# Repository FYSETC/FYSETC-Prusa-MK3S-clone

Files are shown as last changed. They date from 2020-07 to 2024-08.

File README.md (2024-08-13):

# FYSETC-Prusa-MK3S+-clone
FYSETC Prusa MK3S+ clone Kit Database

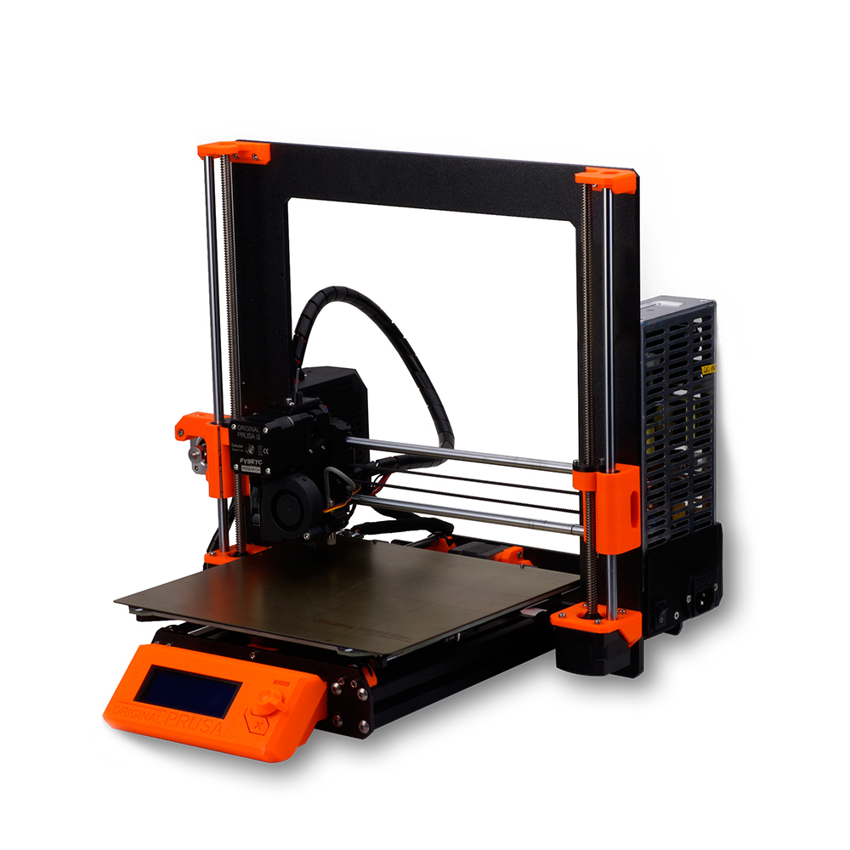
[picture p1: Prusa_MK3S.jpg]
image-Prusa MK3S

1.Prusa MK3S STL file update 2020.7.10
These print files are suitable for FYSETC prusa MK3S 3D printer. Compared with the official printed parts, we have added three parts: PSU-cover-MK3_bottom, PSU-cover-MK3_top, and Spool-holder.The other parts are the same as the official Prusa MK3S. 
You can also get it here：
https://www.thingiverse.com/thing:4728793

2.Prusa MK3S+ assembly tutorial  
<https://help.prusa3d.com/category/original-prusa-i3-mk3s-kit-assembly_1128>

3.Prusa MK3S+ knowledge base  
<https://help.prusa3d.com/en/tag/mk3s+/>

4.Prusa MK3S+ assembly tutorial update 2020.8.3  
The tutorial is very thorough and well explained. We also provide a video tutorial for the assembly process. It is advisable to check both tutorials as you build，below you can watch the video tutorial divided into 5 parts:

https://youtu.be/e2qvbB0Xqfg

https://youtu.be/ntqnIuPzF5k

https://youtu.be/NayX_Eky94o

https://youtu.be/t37JR-865cU

https://youtu.be/UVHUfH4zhIA

5.Go to buy link：https://es.aliexpress.com/item/32968736910.html?spm=a219c.12010615.8148356.3.26ed28558FsEev

# BugFix：
## MK3S+ no Bightness menu fix

### Phenomenon:

Originally, there would be a brightness menu under the setting to adjust the screen backlight, but in fact there isn't;

### Reason:

In order to be more stable during the production of the 2004 screen, we upgraded the triode (BC817) that controls the backlight with a MOS tube (AO3400); The brightness menu will only be available when it is in a low state, so many people who use this screen do not see the brightness menu.

### Solution:

#### 1. Software Method :

Compile the firmware by yourself, and turn off some functions of power-on detection low level.
Open the backlight.cpp file and find the following location:

```cpp
void backlight_init()
{
//check for backlight support on lcd
    SET_INPUT(LCD_BL_PIN);
    WRITE(LCD_BL_PIN,HIGH);
    _delay(10);
    backlightSupport = !READ(LCD_BL_PIN);
    if (!backlightSupport) return;

//initialize backlight
```
Change to：
```cpp
void backlight_init()
{
//check for backlight support on lcd
    SET_INPUT(LCD_BL_PIN);
    WRITE(LCD_BL_PIN,HIGH);
    _delay(10);
    backlightSupport = 1 // !READ(LCD_BL_PIN);// 更改这一行
    if (!backlightSupport) return;

//initialize backlight
```

Then save the file, compile the firmware and download it to the motherboard.

We also provide the compiled firmware on github, copy the following address to the browser to download it directly.

https://github.com/FYSETC/FYSETC-Prusa-MK3S-clone/blob/master/Prusa.mk3s%2B_3.12.rc1_add_brightness.hex

#### 2. Hardware Method :

Replace T1 with a transistor BC817 or BC847 and other compatible NPN transistors. Screens versions produced before 2021 may also need to replace R3 with a 100R resistor.

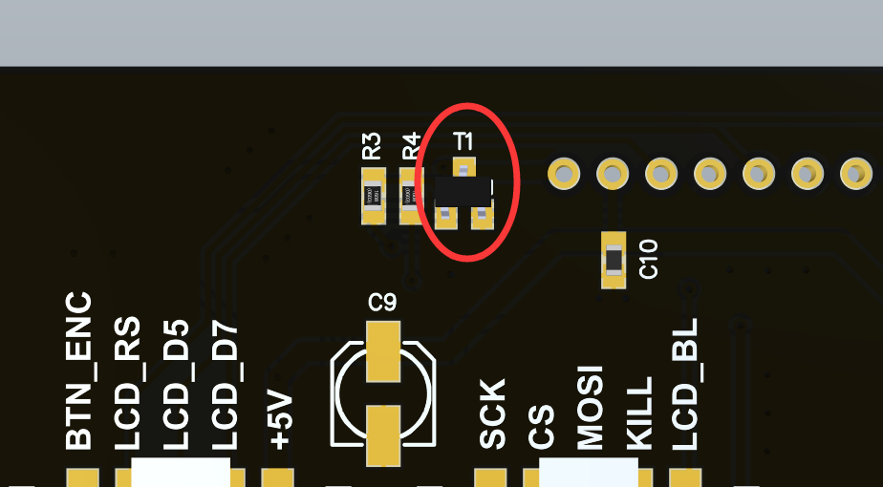
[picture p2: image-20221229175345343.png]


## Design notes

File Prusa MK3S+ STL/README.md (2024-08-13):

# FYSETC Prusa MK3S+ clone
The STLs for the printed parts are from prusa and were made available by them at this link:
<https://www.printables.com/model/57217-i3-mk3s-printable-parts>

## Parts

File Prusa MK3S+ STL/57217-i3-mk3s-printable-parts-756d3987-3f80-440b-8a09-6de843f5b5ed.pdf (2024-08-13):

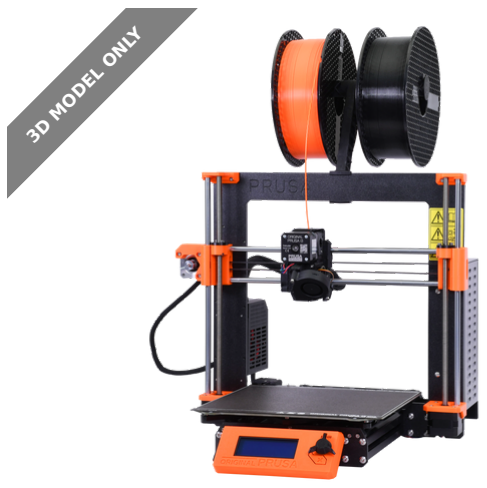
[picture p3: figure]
3D MODEL ONLY

## Summary

Original Prusa i3 MK3S+ printable parts

3D Printers (https://printables.com/model?categoryId=1) | > | Prusa Parts & Upgrades (https://printables.com/model?categoryId=134)
Tags: prusa | i3 | originalprusai3mk3 | mk3s | prusamk3s
parts | prusai3mk3s | originalprusai3mk3s | mk3splus

printableparts

All printable parts for your Original Prusa i3 MK3S+
Sorted by kit assembly manual (http://help.prusa3d.com/en/category/original-prusa-i3-mk3s-kit-assembly_1128) chapters. You can use the file list and folder structure here to prepare parts in the same order as you will need them according to the guide.
Attention, y-rod-holder is present 4 times in the printer. If you plan to print the whole kit, print this part 4x. Look for a number in the brackets in the file description.

### Print instructions

PrusaSlicer's default PETG 0.2mm presets.
For fan-shroud part, we recommend Prusament ASA / PC-Blend with default settings and 5mm brim if necessary.
The fan-shroud STL file includes an inner support rim that needs to be removed after printing. It can be easily removed with needle-nose pliers, a

Prusa Research (https://printables.com/@Prusa3D)

# i3 MK3S+ printable

## parts

VIEW IN BROWSER (https://printables.com/model/57217-i3-mk3s-printable-parts)

updated 13. 11. 2023 | published 13. 11. 2023

knife, or flush cutters together with the brim. Otherwise, it will block most of the air from coming out. See the corresponding assembly manual chapter (https://help.prusa3d.com/en/guide/5-e-axis-assembly_169235#171071) to see what the part should look like after removing the inner support.
ASA, PC Blend, PA or even ABS, as well as other high-temperature materials are only suitable for experienced users, and being from different manufacturers, its properties may vary greatly.
PLA or PET-G is a no-go for fan-shroud because of its low temperature resistance.
We recommend using black filament to print all MK3S+ extruder parts. If you want different colour, you can use it, but the FS-lever part should be definitely dark (black) and the other parts surrounding the IR-Sensor as well. In case you use any lighter colour for the FS-lever it might not trigger the sensor.

# Model files

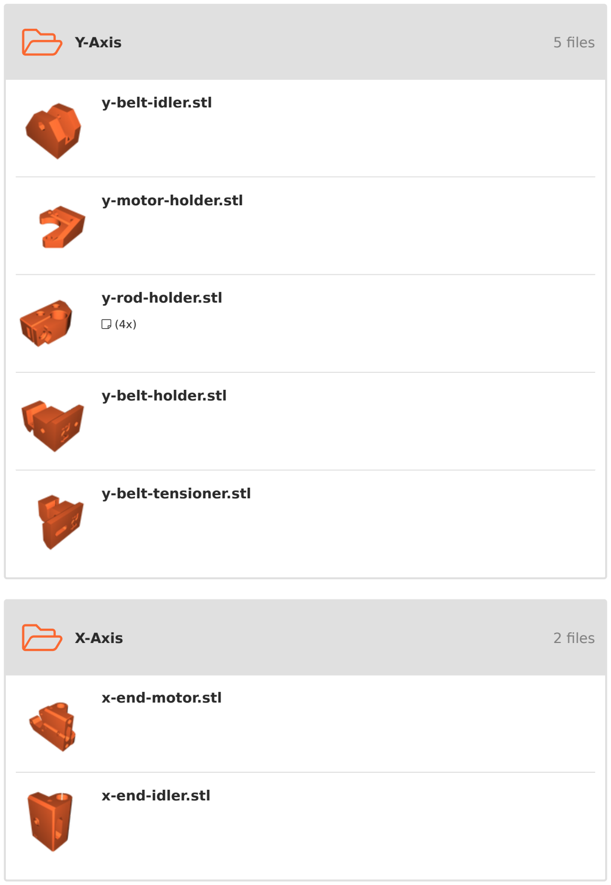
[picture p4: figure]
Y-Axis; 5 files; X-Axis; 2 files; y-belt-idler.stl; y-motor-holder.stl; y-rod-holder.stl; y-belt-holder.stl; y-belt-tensioner.stl; x-end-motor.stl; x-end-idler.stl

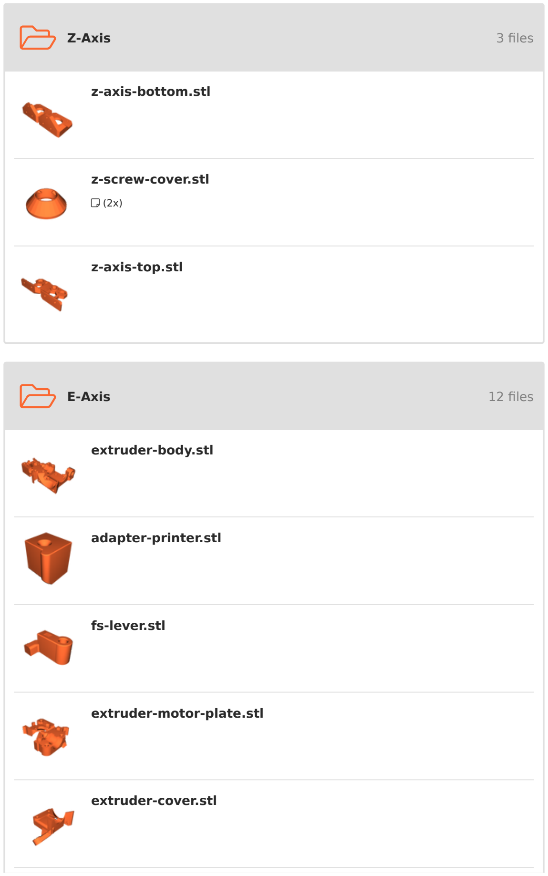
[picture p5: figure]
Z-Axis; 3 files; E-Axis; 12 files; z-axis-bottom.stl; z-screw-cover.stl; z-axis-top.stl; extruder-body.stl; adapter-printer.stl; fs-lever.stl; extruder-motor-plate.stl; extruder-cover.stl

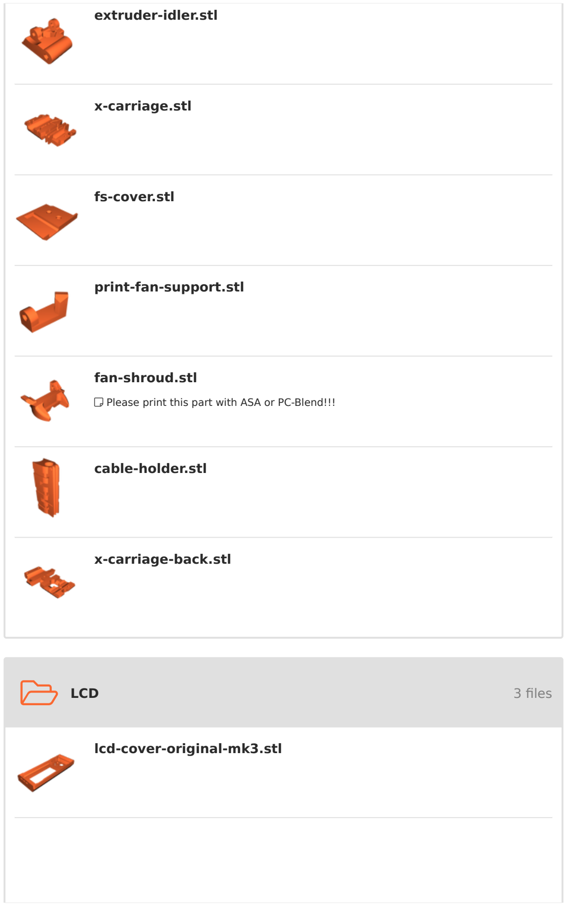
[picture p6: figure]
LCD; 3 files; extruder-idler.stl; x-carriage.stl; fs-cover.stl; print-fan-support.stl; fan-shroud.stl; cable-holder.stl; x-carriage-back.stl; lcd-cover-original-mk3.stl

- Please print this part with ASA or PC-Blend!!!

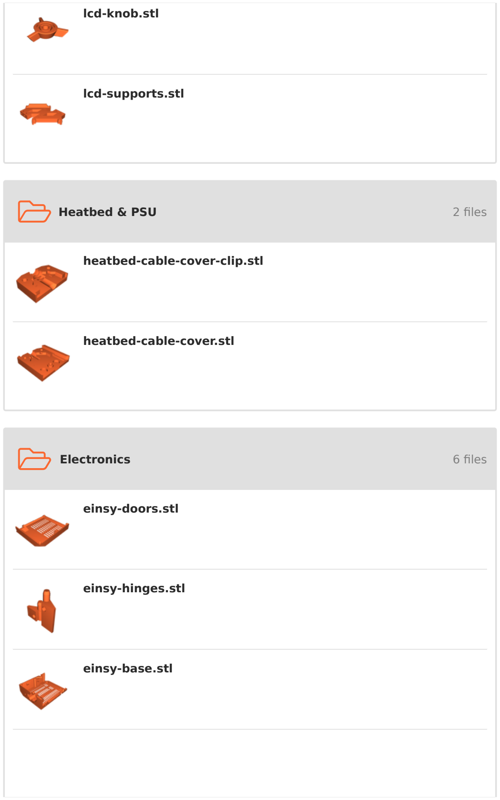
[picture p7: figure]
Heatbed & PSU; 2 files; Electronics; 6 files; lcd-knob.stl; lcd-supports.stl; heatbed-cable-cover-clip.stl; heatbed-cable-cover.stl; einsy-doors.stl; einsy-hinges.stl; einsy-base.stl

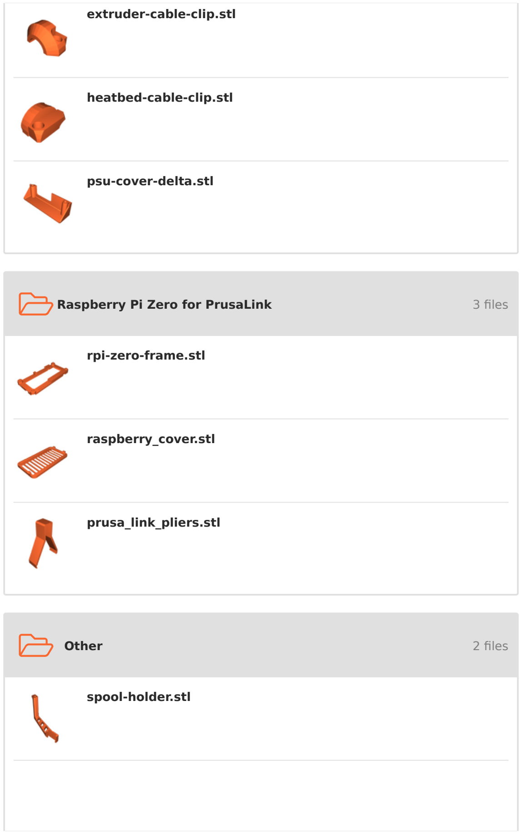
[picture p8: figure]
Raspberry Pi Zero for PrusaLink; 3 files; Other; 2 files; extruder-cable-clip.stl; heatbed-cable-clip.stl; psu-cover-delta.stl; rpi-zero-frame.stl; raspberry_cover.stl; prusa_link_pliers.stl; spool-holder.stl

# Other files

- spare part for the upgraded printers with the silver PSU

## License

This work is licensed under a GNU

General Public License v2.0 (http://www.gnu.org/licenses/old-licenses/gpl-2.0.html)

✖ | Sharing without ATTRIBUTION
✔ | Remix Culture allowed
✔ | Commercial Use
✔ | Meets Open Definition
ℹ | Share under the same license

psu-cover-mk3.stl

howtoprintparts.pdf

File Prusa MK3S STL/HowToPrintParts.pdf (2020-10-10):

# Printing the plastic parts for the Original Prusa i3 MK3S/MK2.5S/MMU2S

Thank you for purchasing the Original Prusa i3 upgrade! Since it will be fully up to you to print the parts, we have decided to prepare a short guide explaining how to do it with ease.
PRINTING THE PLASTIC PARTS FOR THE UPGRADE
By default, you are supplied with a small spool of PETG, but if you are more used to printing with ABS, you can absolutely use it for printing the upgraded parts instead of PETG.

To print all the parts properly, please follow this guide:

1. Clean the print surface with Windex.
2. Download G-codes or .stl files for the upgrade from prusa3d.com/prusa-i3-printable-parts. These G-codes are for PETG only! If you want to prepare your own G-codes, use PETG or ABS settings with at least 20% grid infill.
3. Start the print, wait and observe the first few layers.
4. If you suspect that the first layer does not stick properly, tweak the Live adjust Z value. You can do it from the menu while printing. Press the Knob, select Live adjust Z and then lower the value until the plastic sticks nicely. If object is already detached from the print surface, clean up and start the print again.
5. Once the print is finished, wait until the heatbed cools down to ambient temperature. Do not remove the printed objects right away. Otherwise, you might damage the PEI surface.
6. Once the parts are ready, you can just follow the manual for your printer upgrade available at manual.prusa3d.com.
TROUBLESHOOTING
If you struggle with printing plastic parts, here are some troubleshooting tips to help you out.
- Make sure the print surface is clean. If the Windex didn’t work, try to clean the surface with dish soap water (dish soap water can actually dissolve sugar residue).
- Try to use the bundled glue stick, which increases PEI adhesion for PETG and creates
a separation layer.
- Generate your own G-codes using Slic3r PE. S elect PETG or ABS material with at least 20% grid infill. Place only 2-3 objects around the center of the heated bed for each individual G-code.
- If none of that made any difference, try to start the print and slower the print speed to 70-80%. You can do that by rotating the knob in the counterclockwise direction.

If you have any issues with printing the plastic parts, do not hesitate to contact our support team through Live chat or e-mail info@prusa3d.com.

Scan me

ID 3375

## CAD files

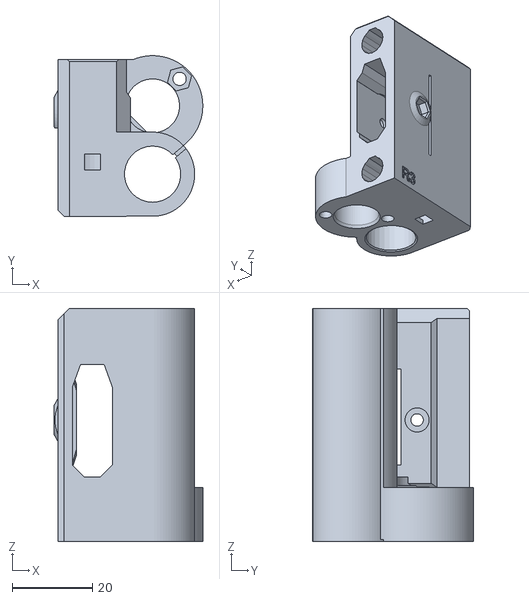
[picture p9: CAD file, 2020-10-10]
Prusa MK3S STL/Orange/x-end-idler.stl
37.0 x 40.0 x 58.0

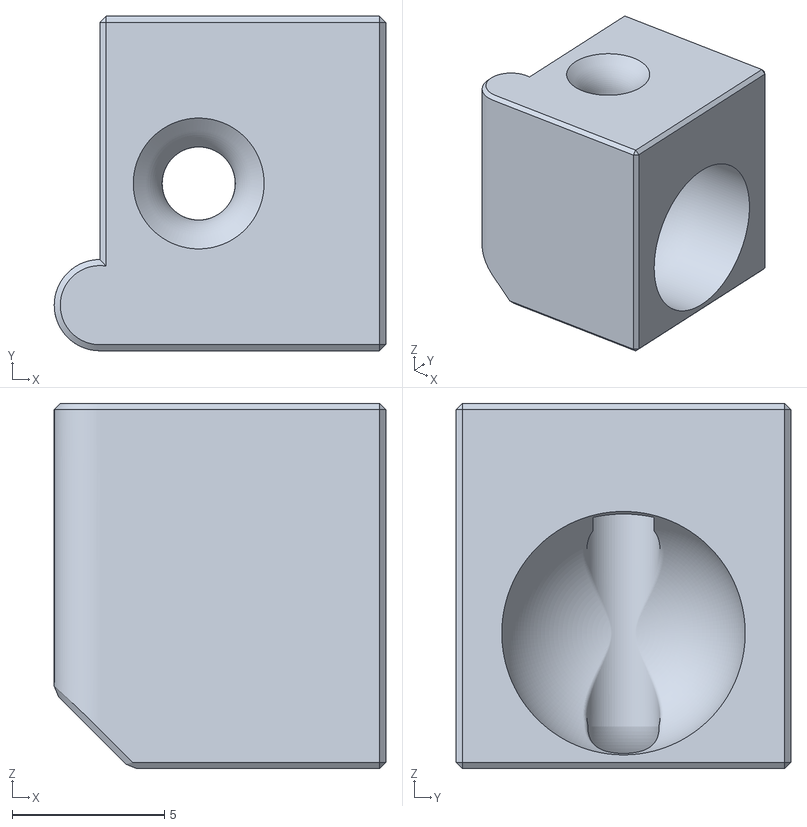
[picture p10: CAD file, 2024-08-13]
Prusa MK3S+ STL/E-Axis/adapter-printer.stl
10.9 x 11.0 x 12.0

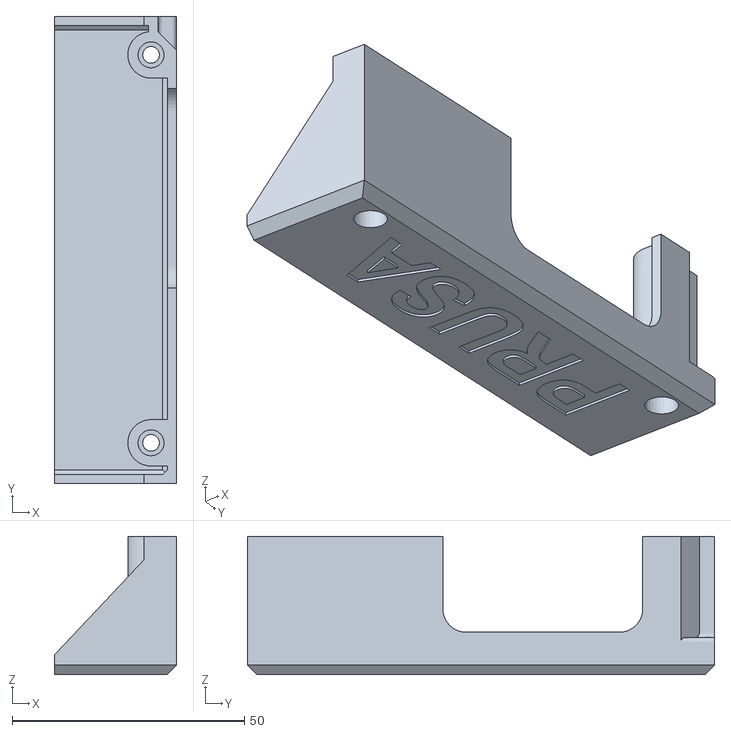
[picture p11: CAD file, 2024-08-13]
Prusa MK3S+ STL/Electronics/psu-cover-DELTA.stl
26.3 x 100.6 x 29.7

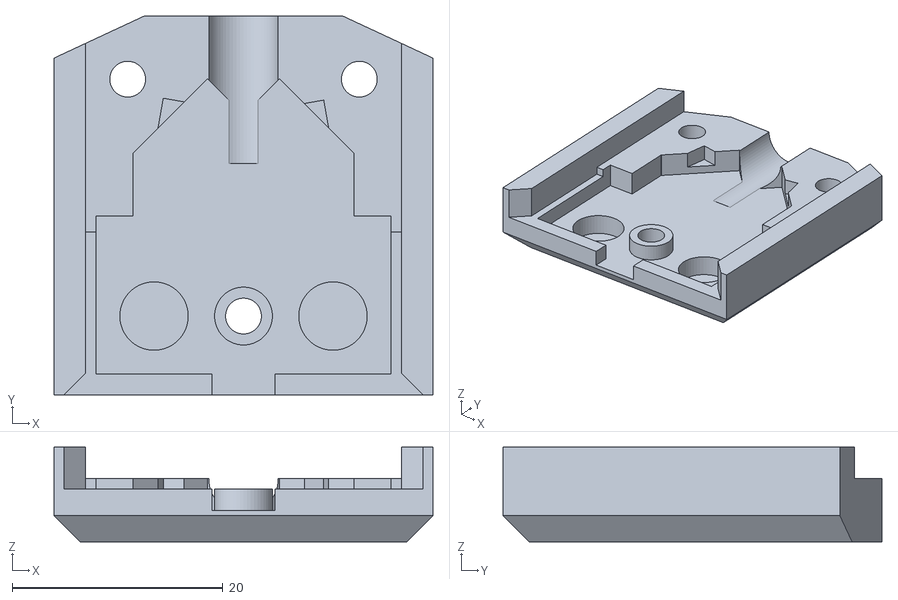
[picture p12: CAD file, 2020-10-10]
Prusa MK3S+ STL/Heatbed & PSU/heatbed-cable-cover.stl
36.0 x 36.0 x 9.00

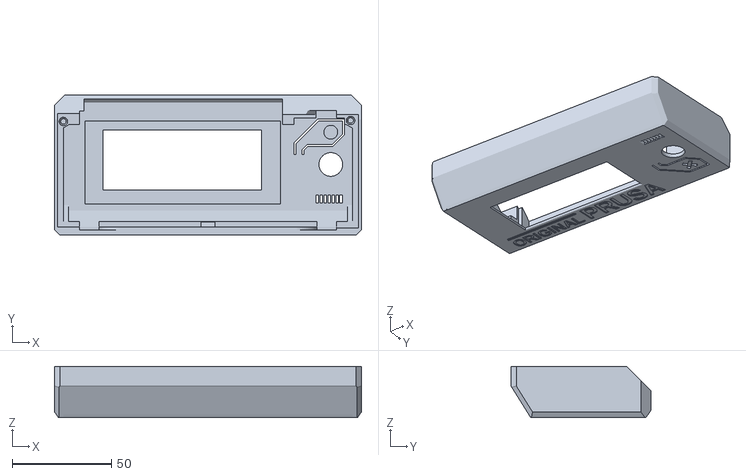
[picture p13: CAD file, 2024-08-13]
Prusa MK3S+ STL/LCD/LCD-cover-ORIGINAL-MK3.stl
155.0 x 70.7 x 26.0

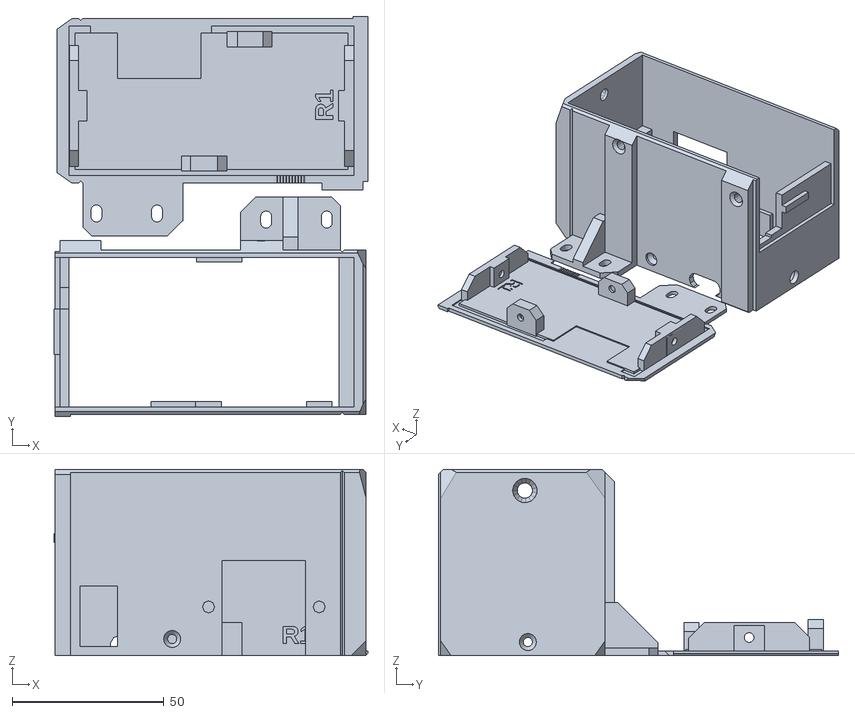
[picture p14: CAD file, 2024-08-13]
Prusa MK3S+ STL/Other/PSU-cover-MK3.stl
103.6 x 132.0 x 61.5

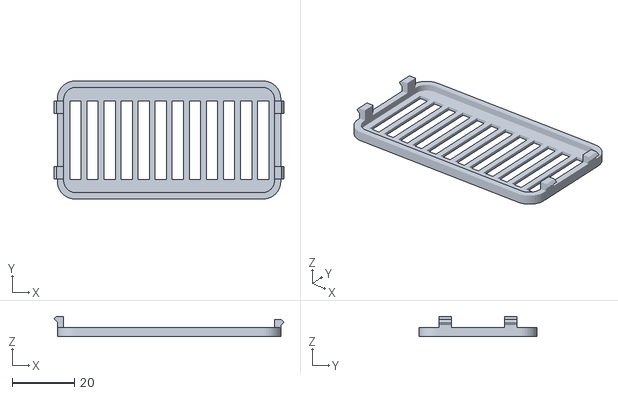
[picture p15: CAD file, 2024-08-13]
Prusa MK3S+ STL/Raspberry Pi Zero for PrusaLink/raspberry_cover.stl
74.1 x 38.0 x 6.50

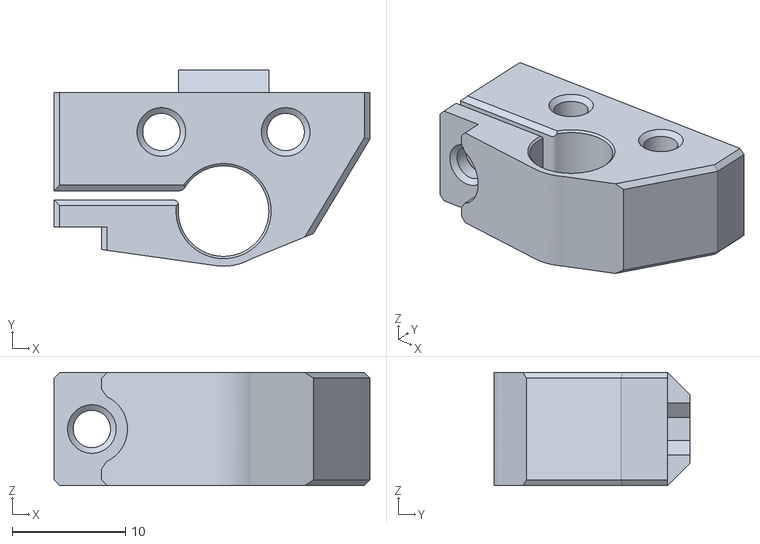
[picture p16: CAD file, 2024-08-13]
Prusa MK3S+ STL/Y-Axis/y-rod-holder.stl
28.0 x 17.4 x 10.0

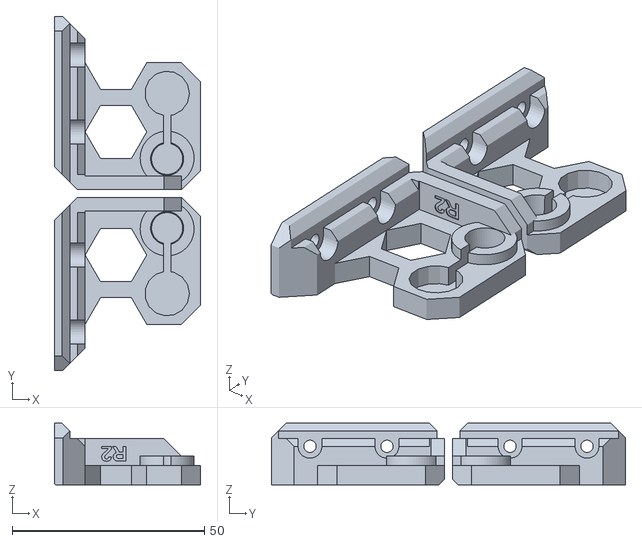
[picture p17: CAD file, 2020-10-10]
Prusa MK3S+ STL/Z-Axis/z-axis-top.stl
38.0 x 92.0 x 16.0

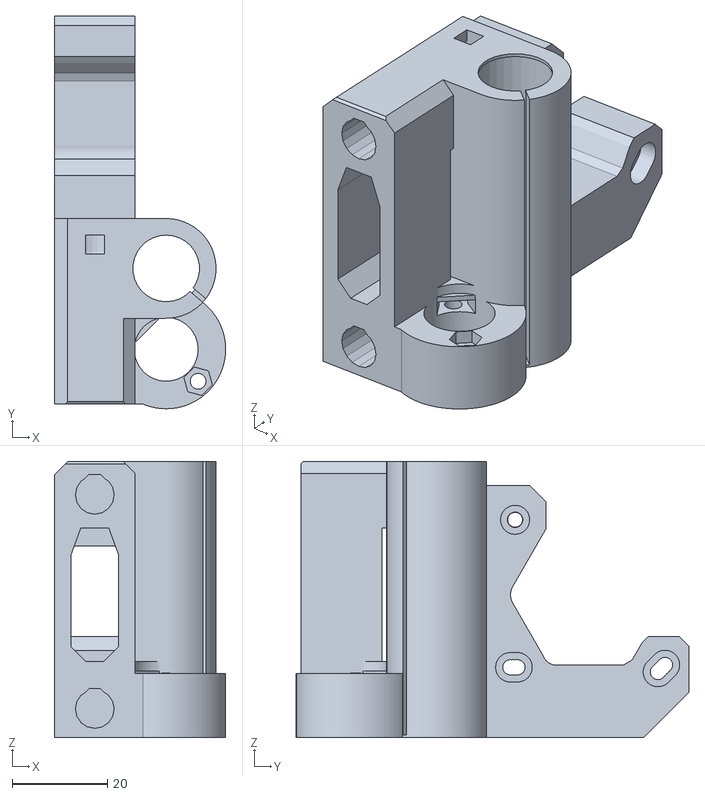
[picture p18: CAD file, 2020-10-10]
Prusa MK3S STL/Orange/x-end-motor.stl
36.0 x 82.5 x 58.0

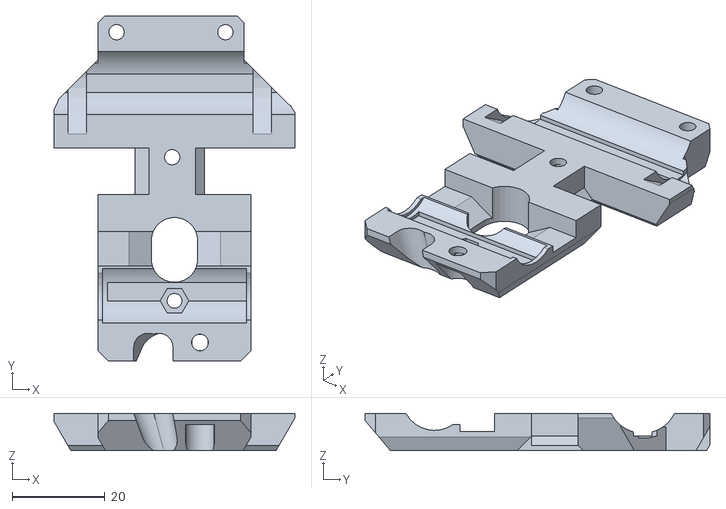
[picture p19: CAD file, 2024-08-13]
Prusa MK3S+ STL/E-Axis/x-carriage-back.stl
52.0 x 74.5 x 8.00

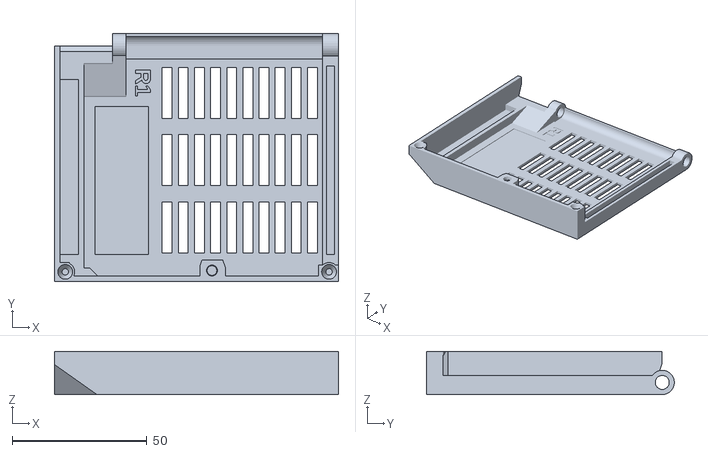
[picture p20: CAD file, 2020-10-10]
Prusa MK3S+ STL/Electronics/Einsy-doors.stl
105.5 x 92.0 x 16.0

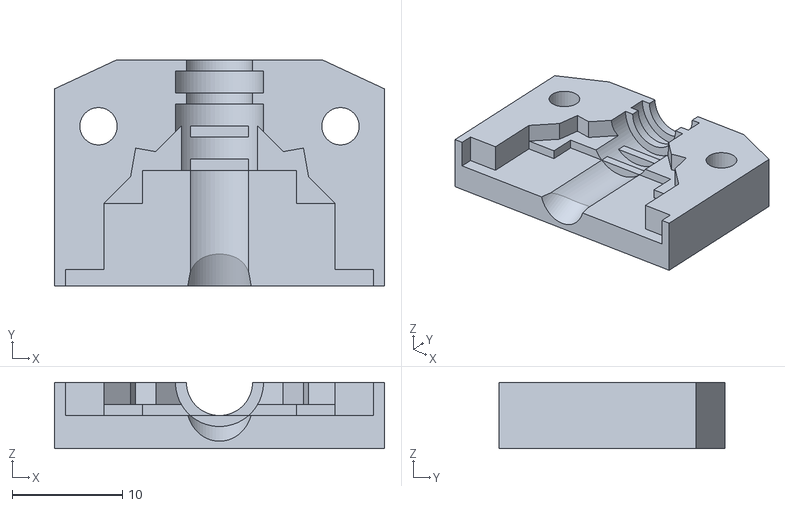
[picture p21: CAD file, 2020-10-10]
Prusa MK3S+ STL/Heatbed & PSU/heatbed-cable-cover-clip.stl
30.0 x 20.5 x 6.00

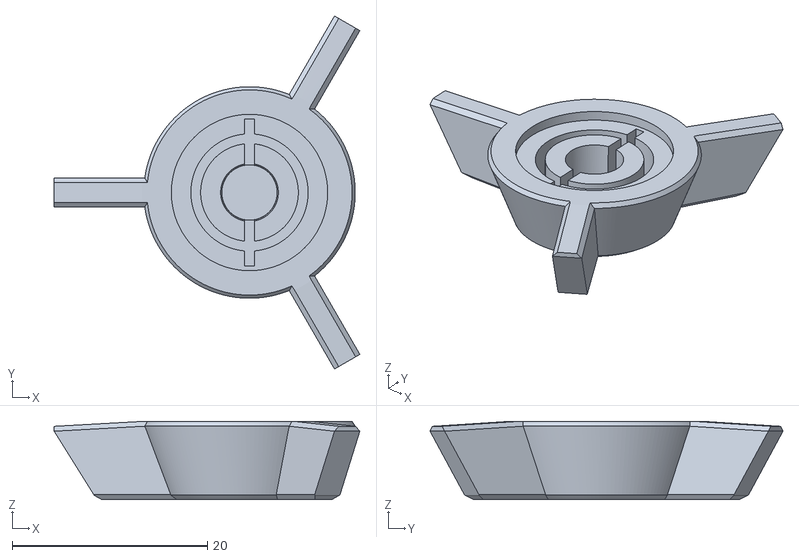
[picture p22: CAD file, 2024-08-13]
Prusa MK3S+ STL/LCD/LCD-knob.stl
31.3 x 36.1 x 8.00

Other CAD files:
Prusa MK3S+ STL/X-Axis/x-end-idler.stl
Prusa MK3S+ STL/Other/Spool-holder.stl
Prusa MK3S+ STL/Raspberry Pi Zero for PrusaLink/rpi-zero-frame.stl
Prusa MK3S+ STL/X-Axis/x-end-motor.stl
Prusa MK3S STL/Orange/LCD-cover-ORIGINAL-MK3.stl
Prusa MK3S STL/Orange/LCD-knob.stl
Prusa MK3S STL/Orange/y-rod-holder.stl
Prusa MK3S STL/black/PSU-cover-MK3_bottom.STL
Prusa MK3S STL/black/PSU-cover-MK3_top.STL
Prusa MK3S STL/black/Spool-holder.STL
Prusa MK3S STL/black/adapter-printer.STL
Prusa MK3S STL/black/extruder-body.stl
Prusa MK3S STL/black/extruder-cover.stl
Prusa MK3S STL/black/extruder-idler.stl
Prusa MK3S STL/black/extruder-motor-plate.stl
Prusa MK3S STL/black/fs-cover.stl
Prusa MK3S STL/black/fs-lever.STL
Prusa MK3S STL/black/plug-aligner.stl
Prusa MK3S STL/black/print-fan-support.stl
Prusa MK3S STL/black/x-carriage-back.stl
Prusa MK3S STL/black/x-carriage.stl
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

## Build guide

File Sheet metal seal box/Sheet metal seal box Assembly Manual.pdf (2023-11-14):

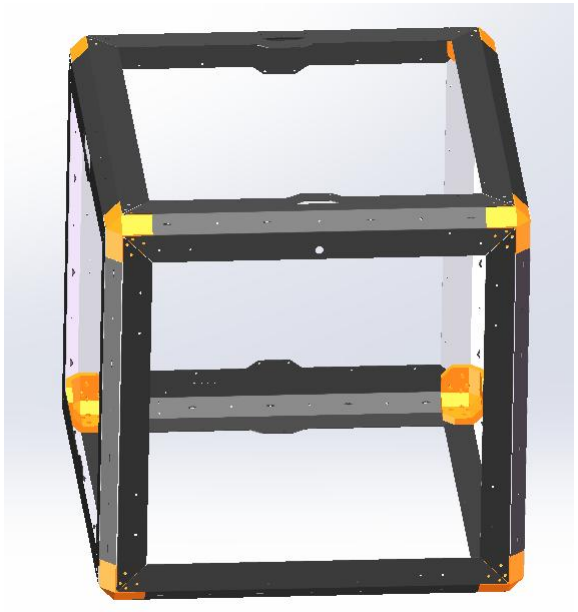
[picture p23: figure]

### Framework

Lower left | Front lower
left | front

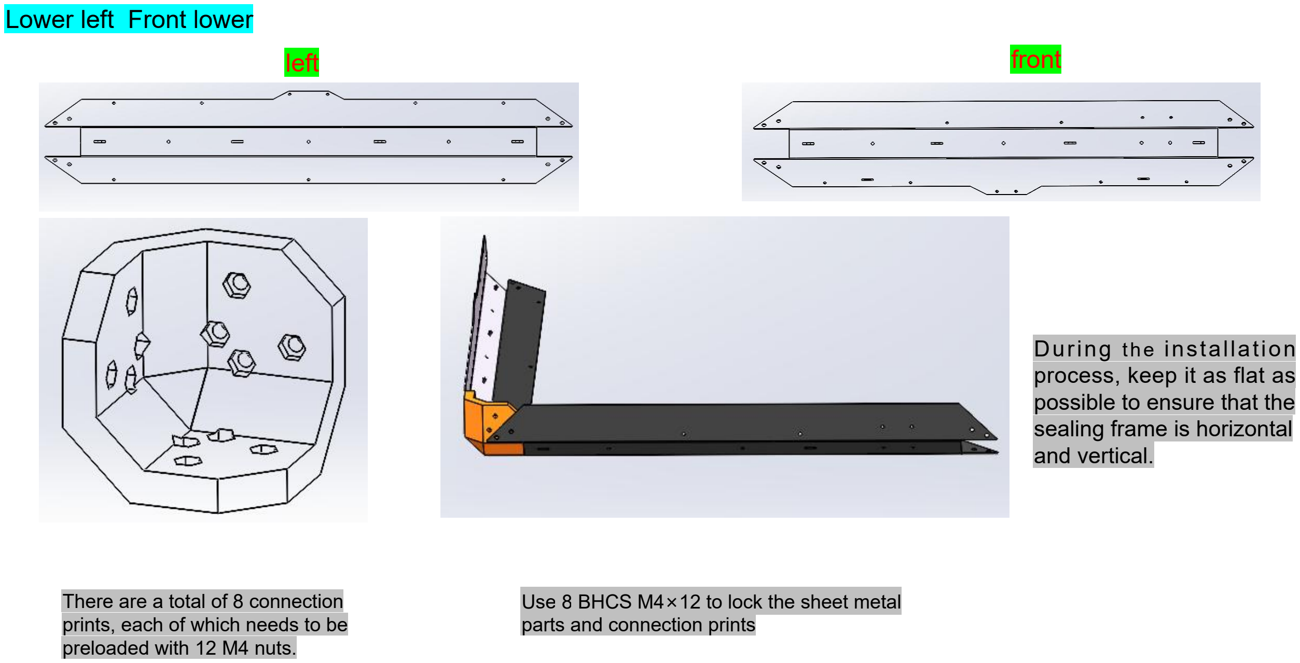
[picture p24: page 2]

There are a total of 8 connection
prints, each of which needs to be
preloaded with 12 M4 nuts. | Use 8 BHCS M4×12 to lock the sheet metal parts and connection prints
During | the | installation
process, keep it as flat as possible to ensure that the sealing frame is horizontal and vertical.

### Lower right

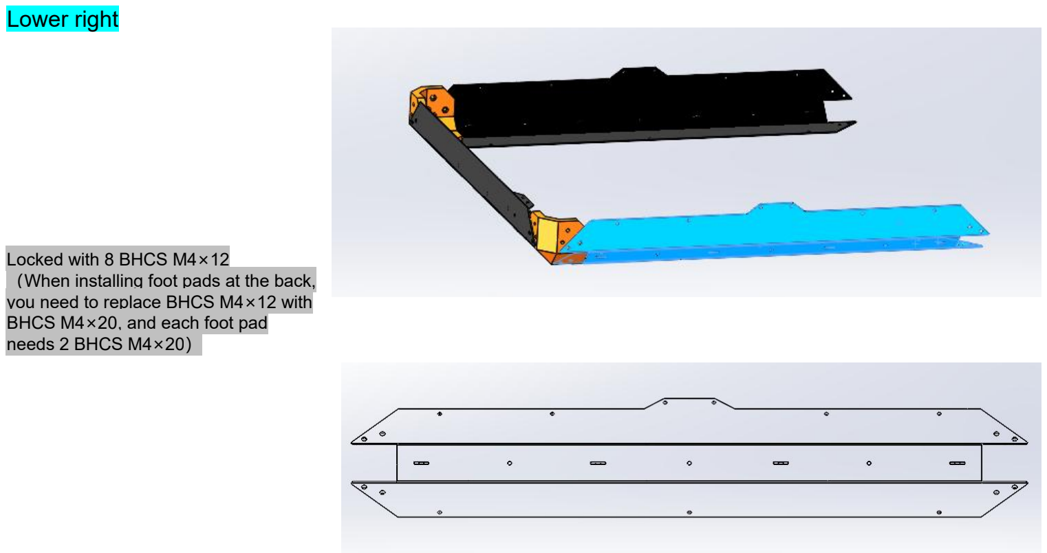
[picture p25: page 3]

Locked with 8 BHCS M4×12
（When installing foot pads at the back, you need to replace BHCS M4×12 with

BHCS M4×20, and each foot pad needs 2 BHCS M4×20）

### Lower back

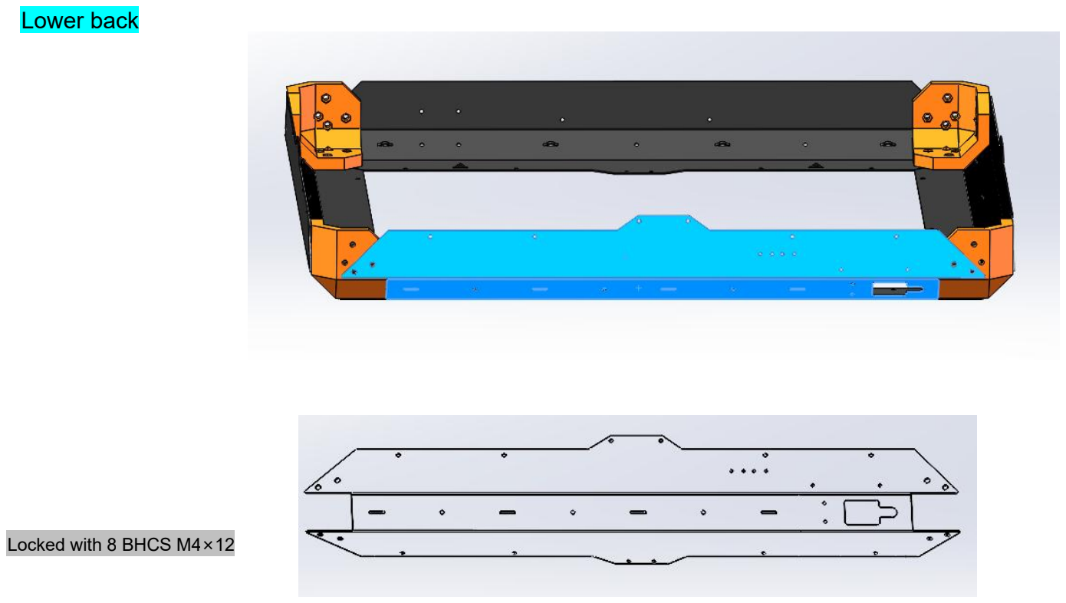
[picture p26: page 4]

Locked with 8 BHCS M4×12

### Front

Left | Right

Locked with 8 BHCS M4×12

### Back

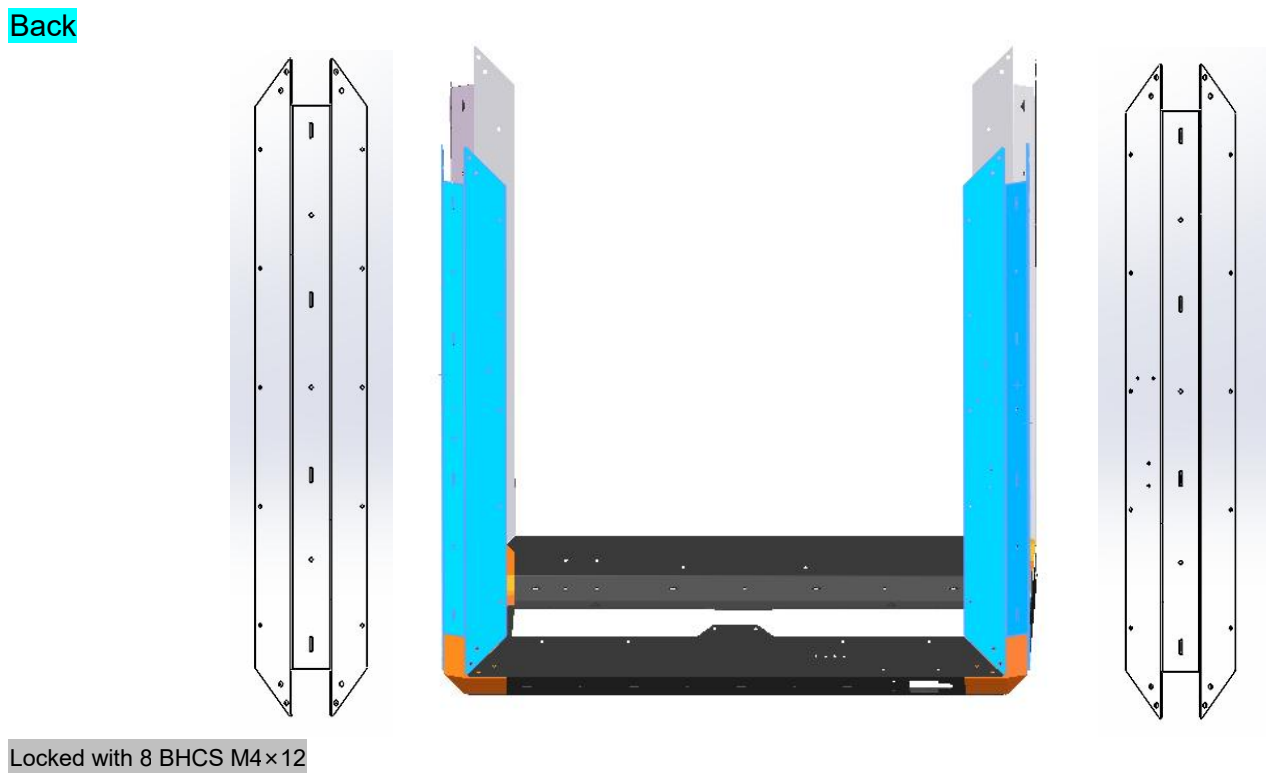
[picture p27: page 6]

Locked with 8 BHCS M4×12

### Front and top

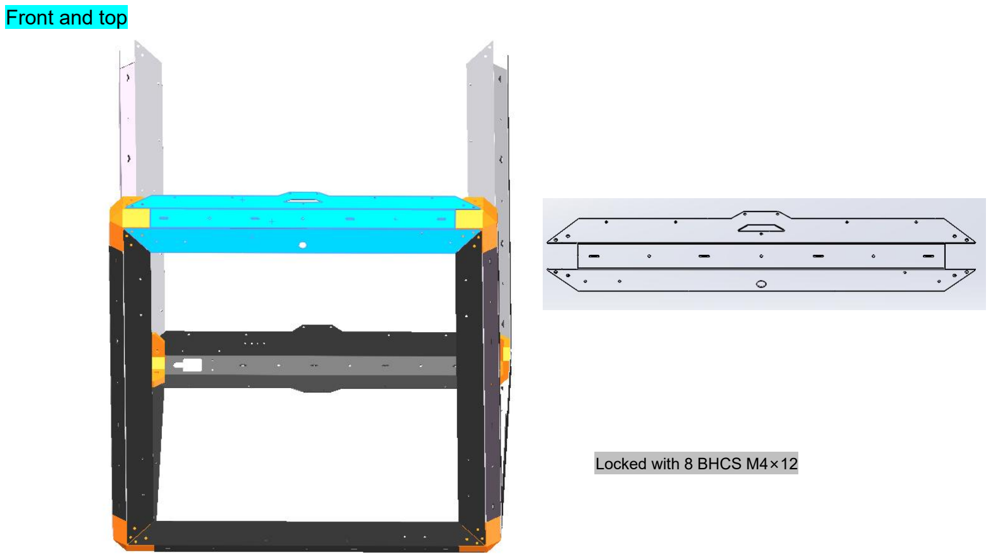
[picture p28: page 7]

Locked with 8 BHCS M4×12

### Upper left

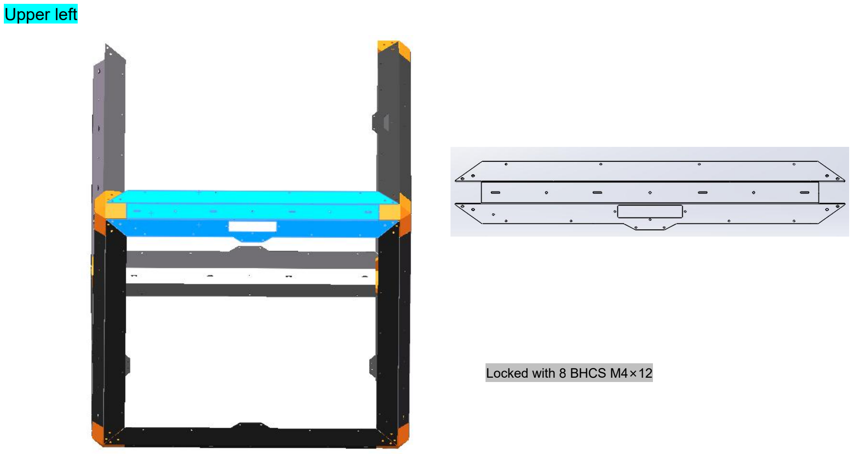
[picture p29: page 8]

Locked with 8 BHCS M4×12

### Upper back

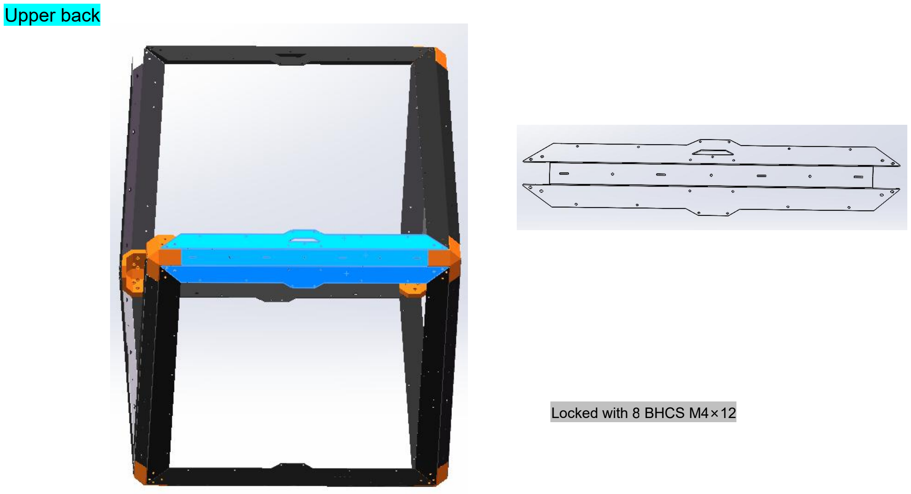
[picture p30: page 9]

Locked with 8 BHCS M4×12

### Upper right

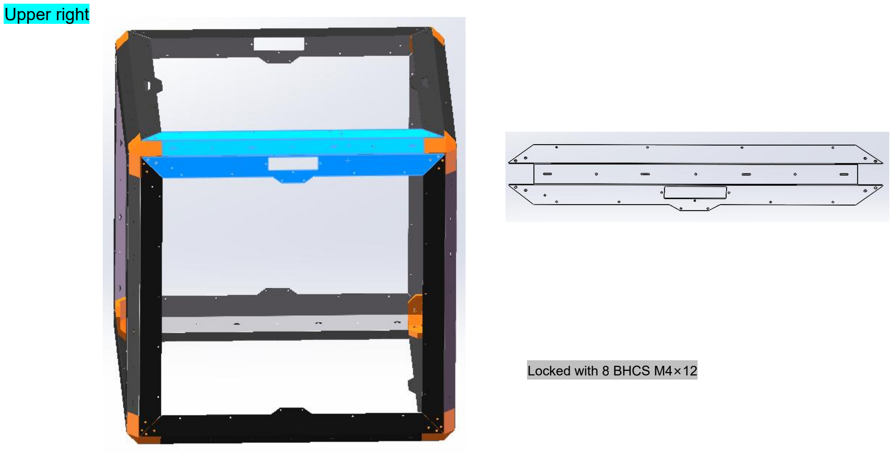
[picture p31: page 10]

Locked with 8 BHCS M4×12

### Bottom plate

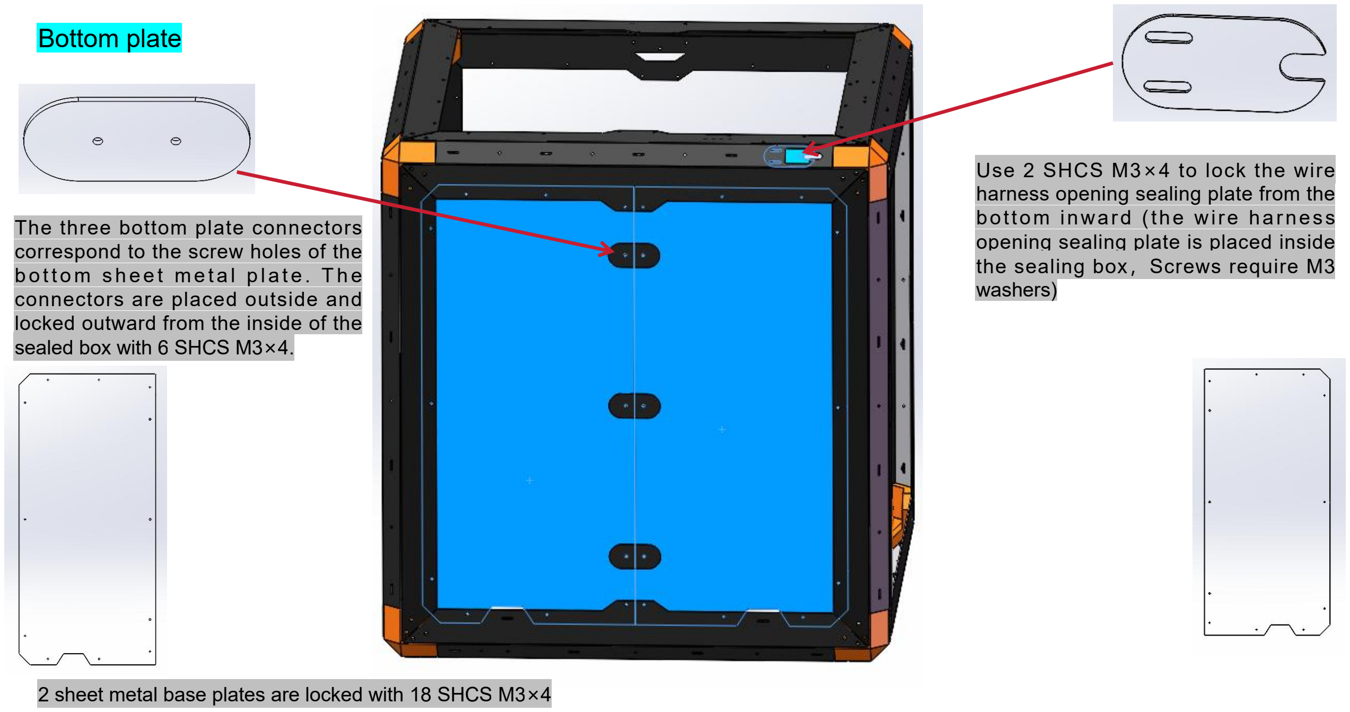
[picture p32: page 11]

The three bottom plate connectors correspond to the screw holes of the b o t t o m s h e e t m e t a l p l a t e . Th e connectors are placed outside and locked outward from the inside of the sealed box with 6 SHCS M3×4.

Use | 2 | SHCS M3×4 | to lock the wire
harness opening sealing plate from the bottom inward (the wire harnes s opening sealing plate is placed inside the sealing box，Screws require M3 washers)

2 sheet metal base plates are locked with 18 SHCS M3×4

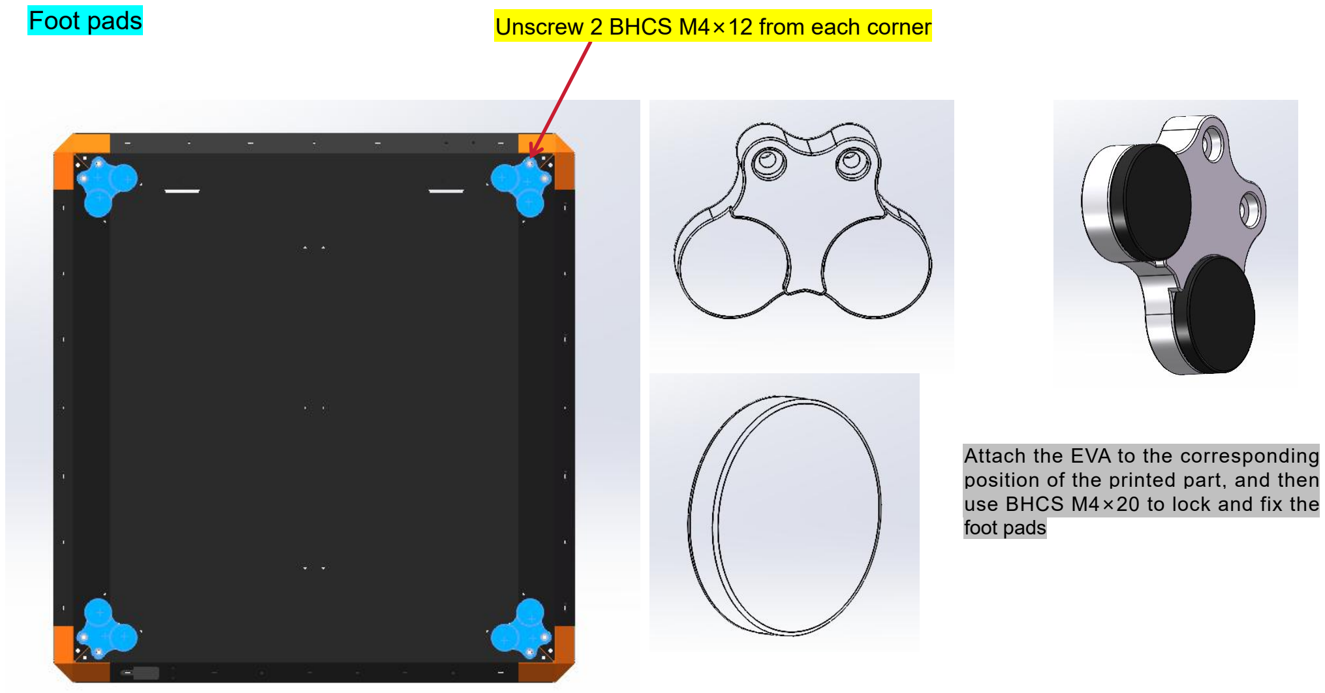
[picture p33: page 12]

Foot pads

Unscrew 2 BHCS M4×12 from each corner

Attach the EVA to the corresponding position of the printed part, and then use BHCS M4×20 to lock and fix the foot pads

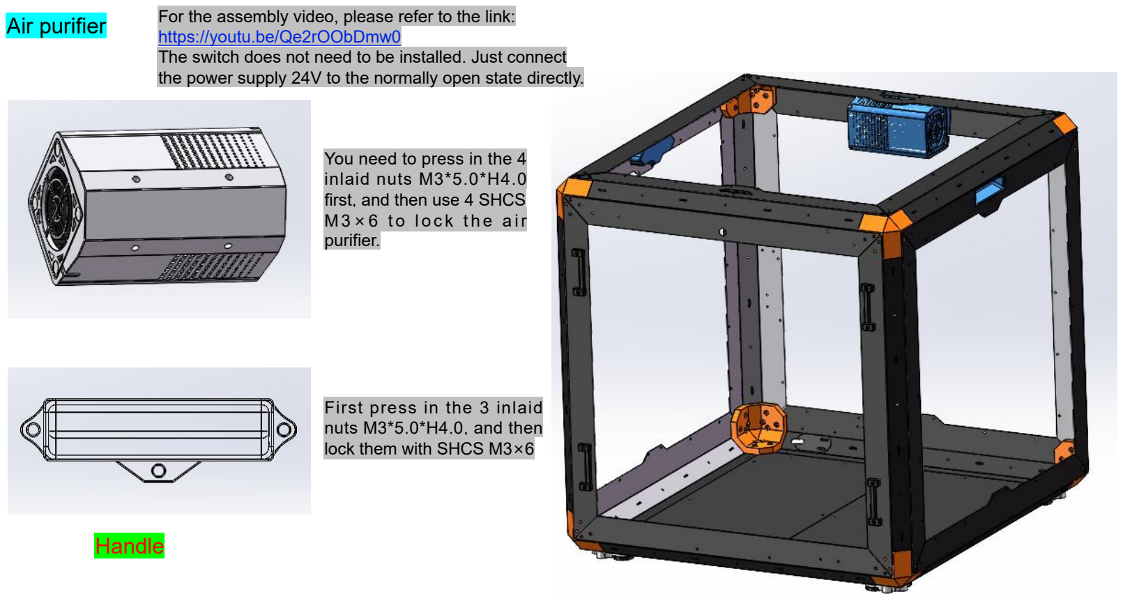
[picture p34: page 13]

Air purifier For the assembly video, please refer to the link: https://youtu.be/Qe2rOObDmw0 The switch does not need to be installed. Just connect the power supply 24V to the normally open state directly. You need to press in the 4

inlaid nuts M3*5.0*H4.0
first, and then use 4 SHCS M 3 × 6 t o l o c k t h e a ir purifier.

### Handle

First press in the 3 inlaid nuts M3*5.0*H4.0, and then lock them with SHCS M3×6

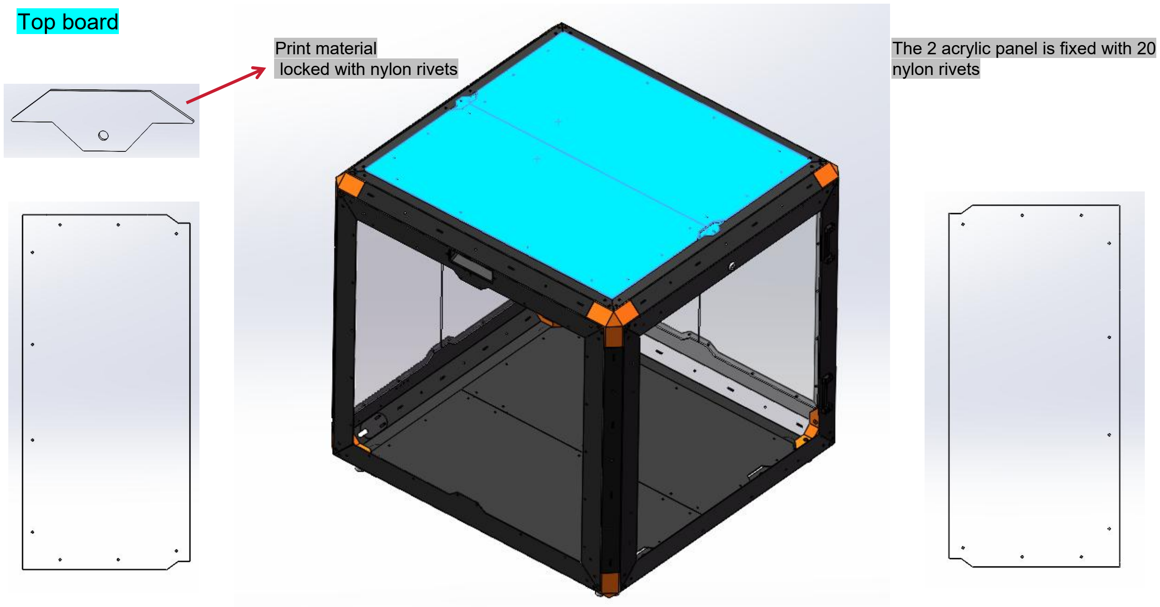
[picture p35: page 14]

Top board | The 2 acrylic panel is fixed with 20 nylon rivets Print material locked with nylon rivets

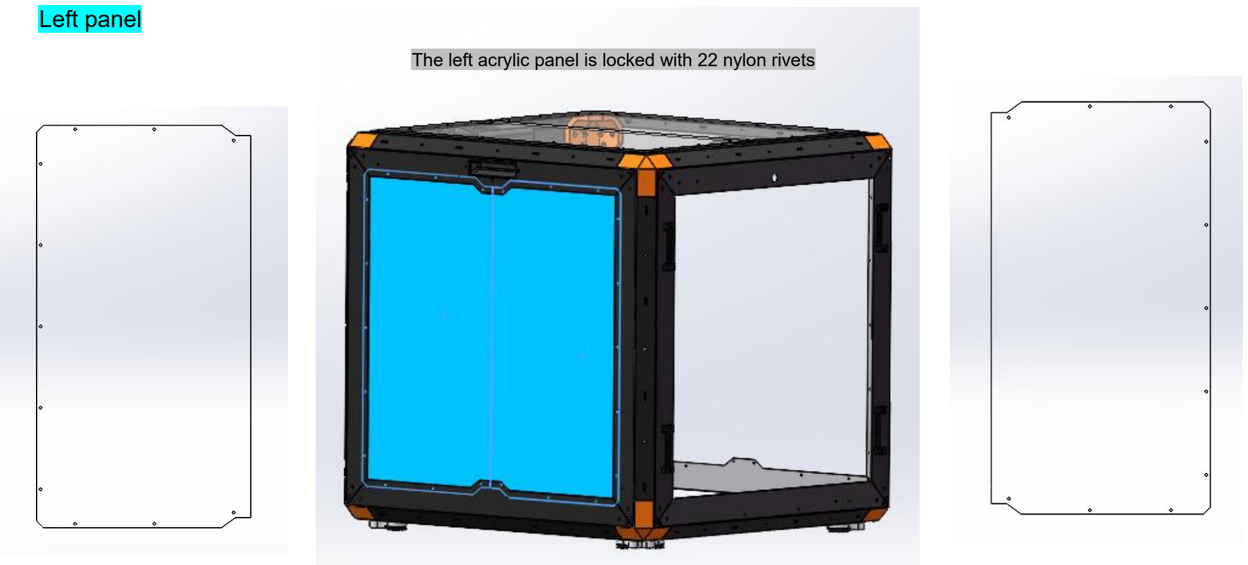
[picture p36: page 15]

Left panel | The left acrylic panel is locked with 22 nylon rivets

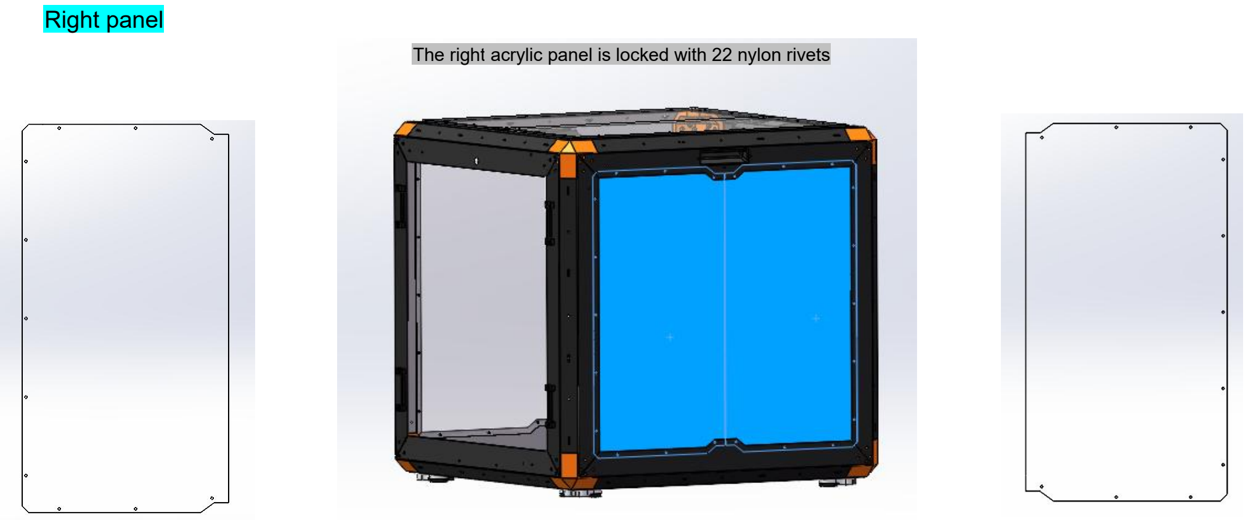
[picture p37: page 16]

Right panel | The right acrylic panel is locked with 22 nylon rivets

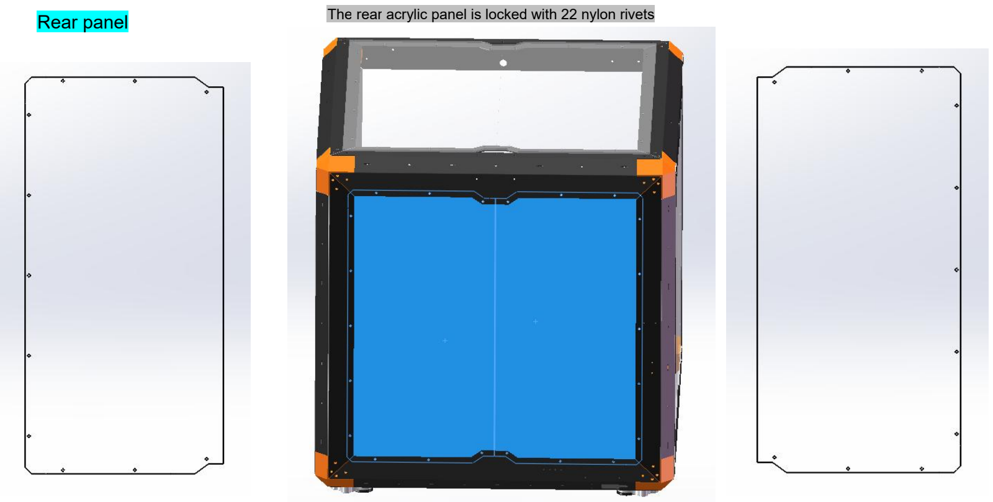
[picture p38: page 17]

Rear panel | The rear acrylic panel is locked with 22 nylon rivets

### Door

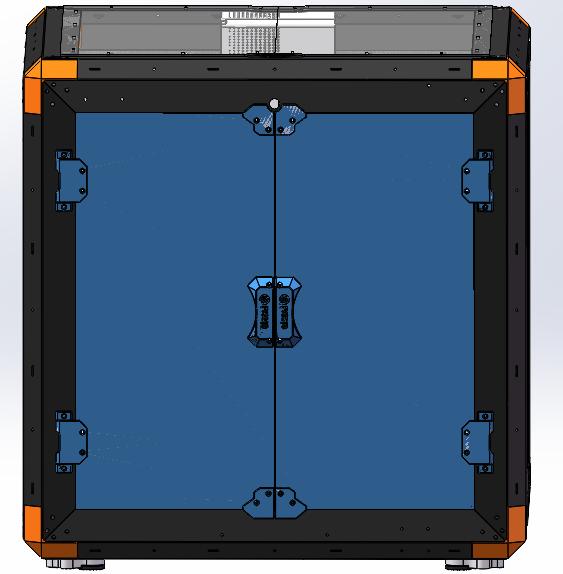
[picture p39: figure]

The printed parts used on the door need to be pre-installed with nuts in advance.

Front view | Right side view

### Left door

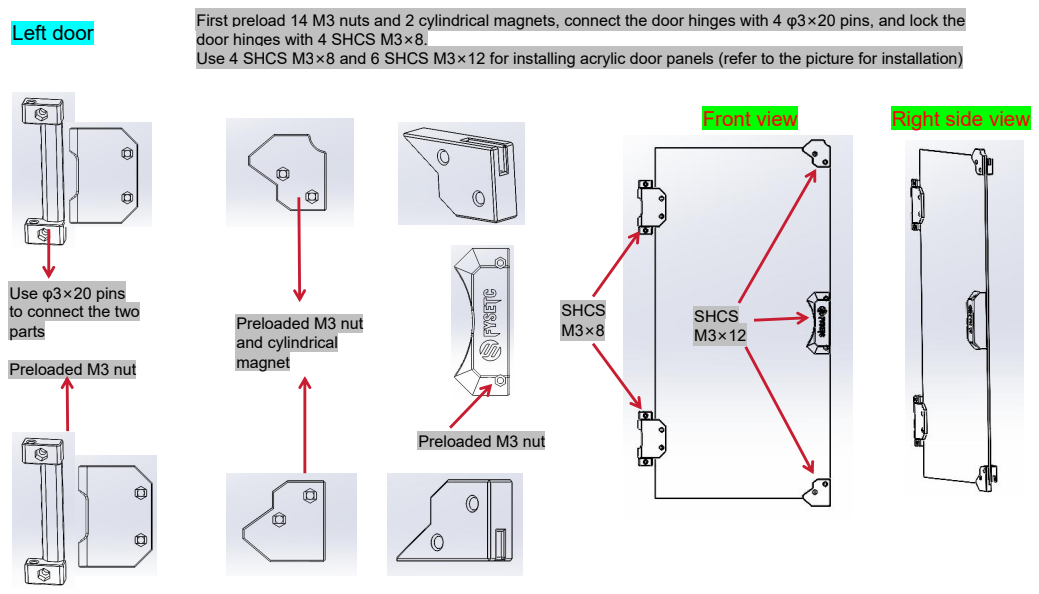
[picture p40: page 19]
Preloaded M3 nut and cylindrical magnet; Preloaded M3 nut; SHCS M3×8; SHCS M3×12

First preload 14 M3 nuts and 2 cylindrical magnets, connect the door hinges with 4 φ3×20 pins, and lock the
door hinges with 4 SHCS M3×8. Use 4 SHCS M3×8 and 6 SHCS M3×12 for installing acrylic door panels (refer to the picture for installation)

Use φ3×20 pins
to connect the two
parts
Preloaded M3 nut

### Right door

Front view | left side view

Use φ3×20 pins
to connect the two
parts

Preloaded 4 M3
nut

First preload 14 M3 nuts and 2 cylindrical magnets, connect the door hinges with 4 φ3×20 pins, and lock the door hinges with 4 SHCS M3×8. Use 4 SHCS M3×8 and 6 SHCS M3×12 for installing acrylic door panels (refer to the picture for installation)

Preloaded 4 M3
nut and cylindrical
magnet Preloaded
SHCS | 2 | M3 nut
M3× 8

SHCS
M3×12

### Humidity Thermometer Door Lock

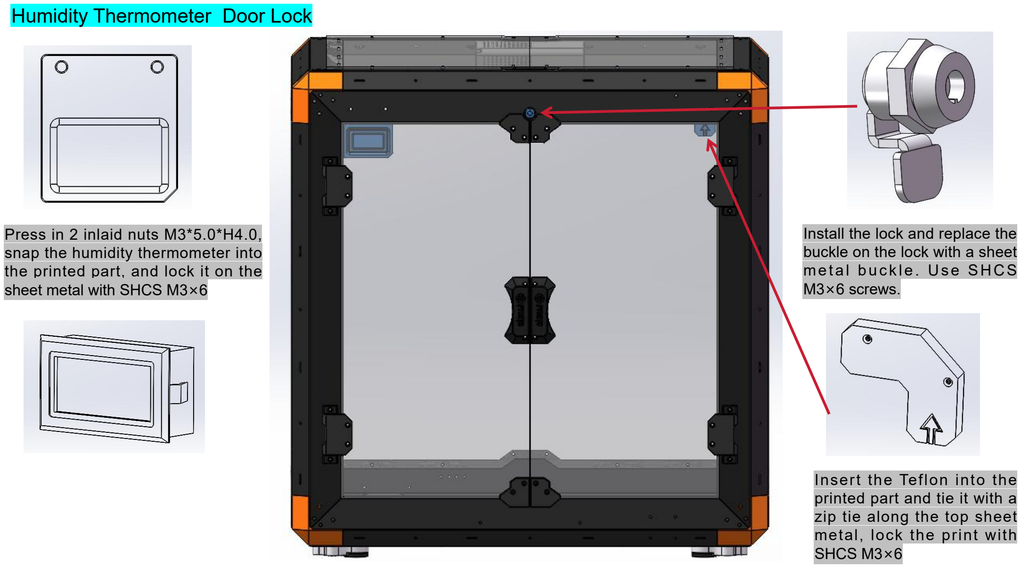
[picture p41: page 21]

Press in 2 inlaid nuts M3*5.0*H4.0, snap the humidity thermometer into

the printed part, and lock it on the sheet metal with SHCS M3×6

Install the lock and replace the buckle on the lock with a sheet met al buc k le. Use SHCS
M3×6 screws.

Insert the Teflon into the printed part and tie it with a zip tie along the top sheet metal, lock the print with SHCS M3×6

Left | Right

### Wiring diagram

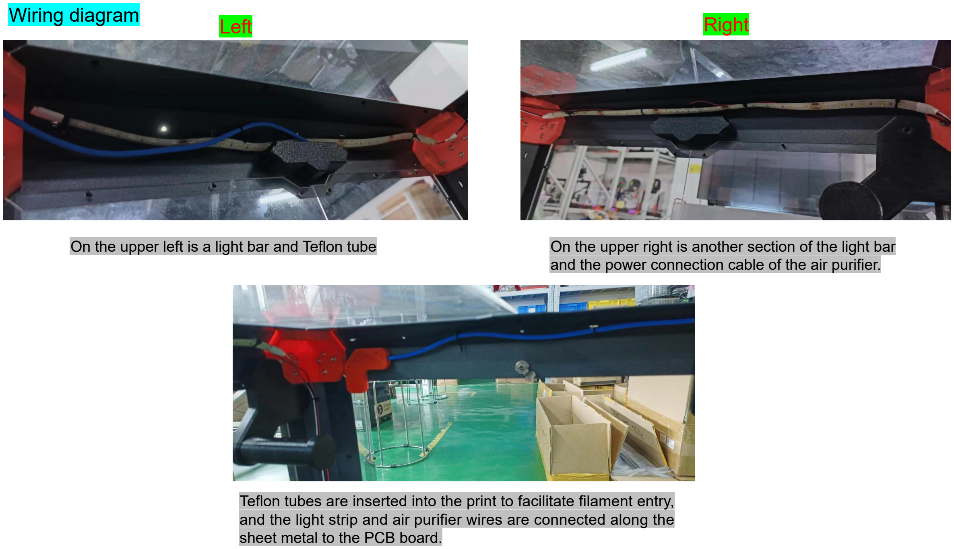
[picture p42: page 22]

On the upper left is a light bar and Teflon tube | On the upper right is another section of the light bar and the power connection cable of the air purifier.

Teflon tubes are inserted into the print to facilitate filament entry, and the light strip and air purifier wires are connected along the

sheet metal to the PCB board.

### Wiring diagram

### Air purifier line interface Light strip line interface

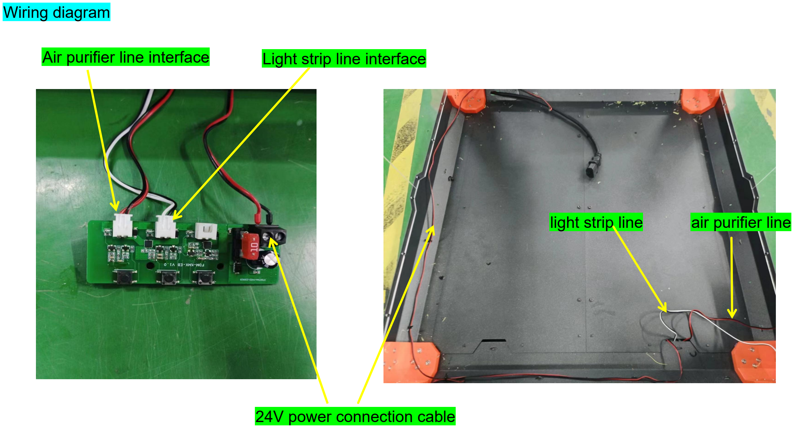
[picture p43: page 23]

### 24V power connection cable

### light strip line air purifier line

### PCB board box, material rack, tool box

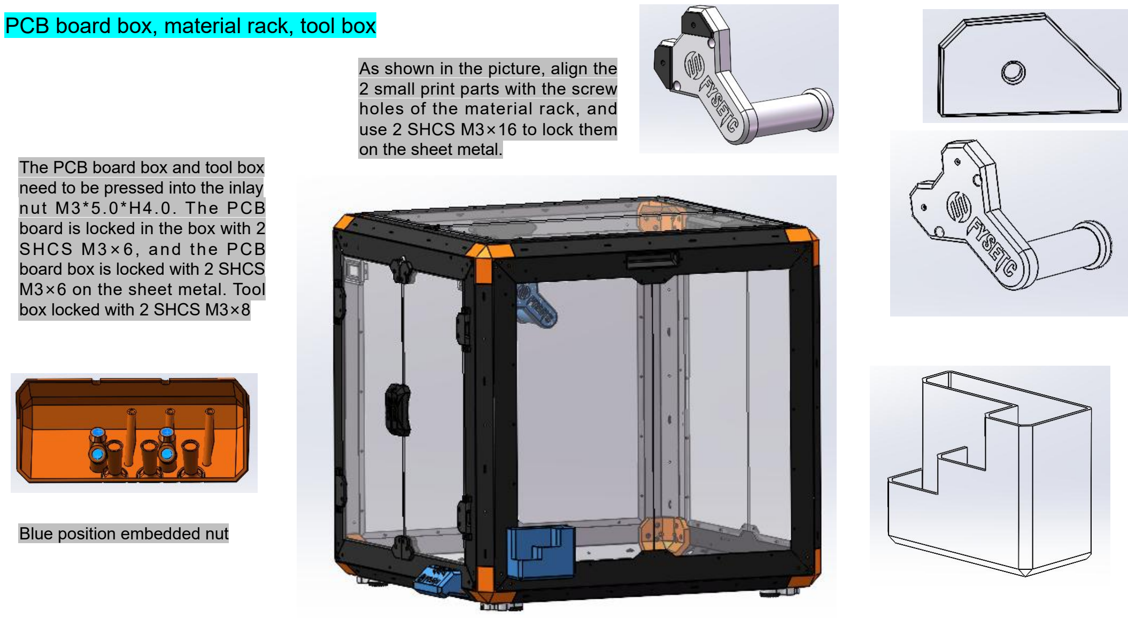
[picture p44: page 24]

The PCB board box and tool box need to be pressed into the inlay nut M3*5.0*H4.0. The PCB
board is locked in the box with 2 SHCS M3×6, and the PCB
board box is locked with 2 SHCS M3×6 on the sheet metal. Tool box locked with 2 SHCS M3×8

Blue position embedded nut

As shown in the picture, align the 2 small print parts with the screw holes of the material rack, and use 2 SHCS M3×16 to lock them on the sheet metal.

### Motor bracket

### top

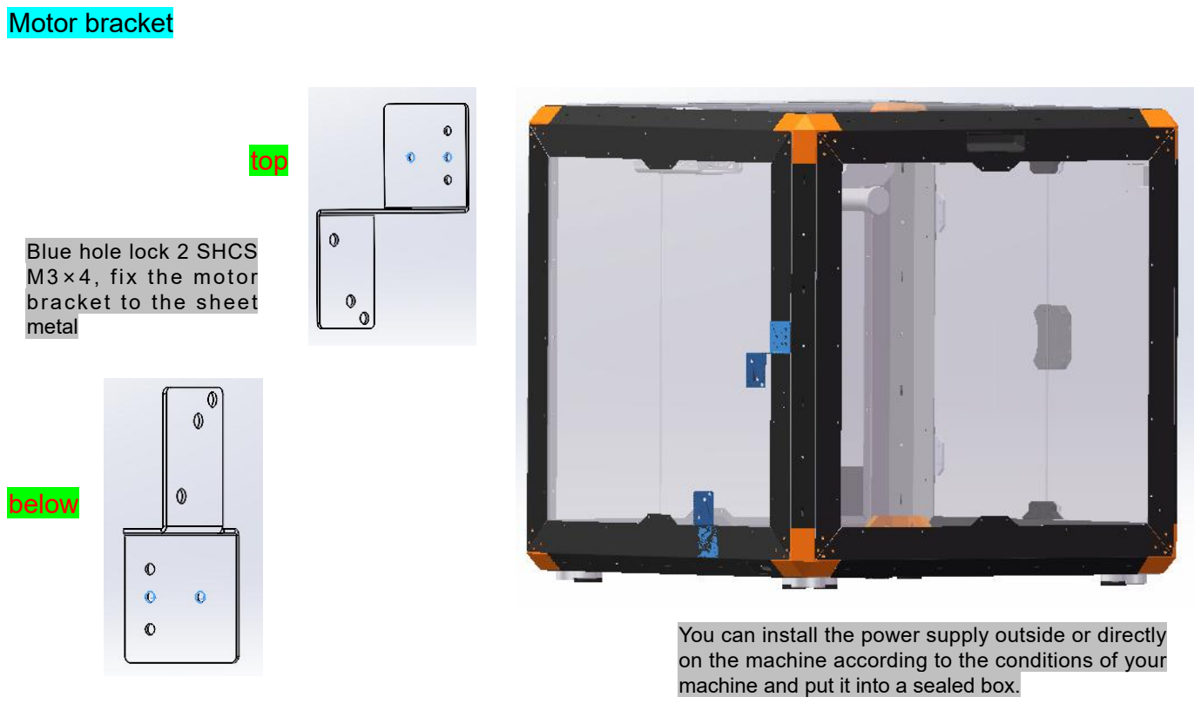
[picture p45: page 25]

### below

Blue hole lock 2 SHCS
M3×4, fix the motor
bracket to the sheet
metal

You can install the power supply outside or directly on the machine according to the conditions of your machine and put it into a sealed box.

### Panorama

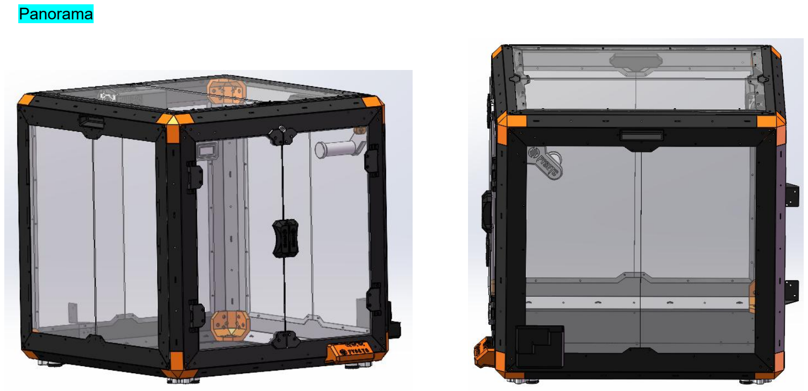
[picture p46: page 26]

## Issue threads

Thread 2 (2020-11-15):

What are the correct settings to print the PSU cover?

chilman408, 2020-11-15:
There seem to be a lot of bridges and need some support.  Be nice to have some instructions here.

stefanomn, 2020-12-27:
i have see some video in youtube and i think dont need to print psu cover if u buy this printer clone.

stefanomn, 2020-12-27:
now i print all other part and will see.

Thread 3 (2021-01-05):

Einsy-base

stefanomn, 2021-01-05:
the Einsy-base stl file is different  in your video you dont have problem to assemble board whit
heatsink  https://www.youtube.com/watch?v=UVHUfH4zhIA
but now whit this news stile the heatsink go to close whit plastic ....
dont have original file of before ..of the video ??

HoganZeng666, 2021-01-06:
Our motherboard has a heat sink than the official motherboard. If you use a new enclosure, the radiator next to it is not installed. Or you use the previous version of the shell. We will change to a shorter radiator in the future so that it can fit into the new enclosure.

stefanomn, 2021-01-06:
thk for your reply... now i have print old  version but is not easy find the old file in github of this case.... maybe is better if you upload in your github seccond version of einsy-base printer files ;)

stefanomn, 2021-01-06:
and maybe if u have time... fork the firmware and fix temperature for your termistor and throat whit ptfe

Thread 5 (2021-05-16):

FYSETC PCB Magnetic Heated Bed 400x400 Eli Wong

odellmar, 2021-05-16:
This question is for FYSETC. Trying to contact either Eli Wong or George Fu about the production of a bigger Heated Bed to my Design and Specifications. This question is Directed to @george @eliwong

GerogeFu, 2021-05-17:
Hey , you can contact me with email fzl@fysetc.com

Blade765, 2021-05-17:
I too would be interested in a bed of this size from you guys!

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

--
Kindest Regards,
Tristan N. Gatineau

odellmar, 2021-05-18:
@Blade765 I'm working with FYSETC on a design. What machine are you needing this for?

Blade765, 2021-05-18:
A Voron, scaled up to fit a 400x400 bed

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

odellmar, 2021-05-18:
@Blade765 Which model? Are you already printing on 400X400, how is it attached?

Blade765, 2021-05-18:
The 2.4. I haven't come up with a way to attach it (yet). I only just
discovered they were even possible, thanks to you and Fysetc. All I buy is
Fysetc stuff, I love and trust their quality.

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

odellmar, 2021-05-19:
@Blade765 I'm in the process of building a 400X400X420 PRUSA i3 MK3S+ . The Heated bed I'm designing will be held to the Y-Carriage the same as the PRUSA with 5 screws, one in the center and 4 at each corner. How is the bed attached on your 2.4?

Ollie

odellmar, 2021-05-19:
@Blade765 Do you have a means for more direct contact?

odellmar, 2021-05-20:
@Blade765 Did you receive E-mail?

Blade765, 2021-06-20:
Ollie,
My apologies!! Things have been insanely busy, and I didn't see your
replies until now. I'm not entirely sure how the bed attaches to the
Voron's, as I haven't gotten to that point of the build.

I can be reached on Discord at Blade765#4758 if you prefer?

Tristan

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

--
Kindest Regards,
Tristan N. Gatineau

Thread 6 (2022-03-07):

New Firmware ?

hdano1, 2022-03-07:
Can you upload newer firmware , then the one in clone board?
(prusa3d_fw_MK3S_3_9_3_3556.hex)
thx

hdano1, 2022-11-17:
Typical chinese seller, just sell and no care later.

darxx1, 2023-02-12:
hi, since there are no new builds from the Fysetc website, I decided to compile the new firmware for the Prusa clone myself. This is a stable build for the Bear extruder. For the original extruder I will post soon. Please follow my github:

https://github.com/darxx1/FYSETC-Prusa-MK3S-Bear-Brightness

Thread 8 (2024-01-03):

PSU Holder

suprchunk, 2024-01-03:
In the Bear kit, you include two orange, printed, PSU holders to attach the PSU to the frame. These are not in the STL folder on this site, you also do not list them on your site.

Can you please provide the files so that we can print these in something else besides that gross orange?

Thank you!

suprchunk, 2024-01-20:
PSU holders? You include the orange printed ones in the kit, but do not provide an STL so that I can have a non-orange colored version one.

Are you going to provide this file? Otherwise this kit is incomplete and I cannot recommend it.

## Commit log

2020-07-10 Hoganzen
    Add STL printing parts, tutorial URL, knowledge base URL.
    [Einsy Base 2.STL, Einsy-hinges1.STL, Einsy-hinges2.STL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]
2020-10-10 Update print parts
    Update print parts
    [Einsy Base 2.STL, Einsy-base.stl, Einsy-doors.stl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]
2023-11-14 Add Assembly Manual
    Add Sheet metal seal box Assembly Manual
2024-08-13 Added MK3S+ STLs
    Added a folder with the MK3S+ files
    [Einsy-base.stl, Einsy-doors.stl, Einsy-hinges.stl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]
